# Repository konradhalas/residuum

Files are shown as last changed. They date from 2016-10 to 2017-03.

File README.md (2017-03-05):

# Residuum - line following robot



Residuum is a line following robot. It's a simple construction based on the Arduino board, an array of eight reflectance sensors and two DC motors.

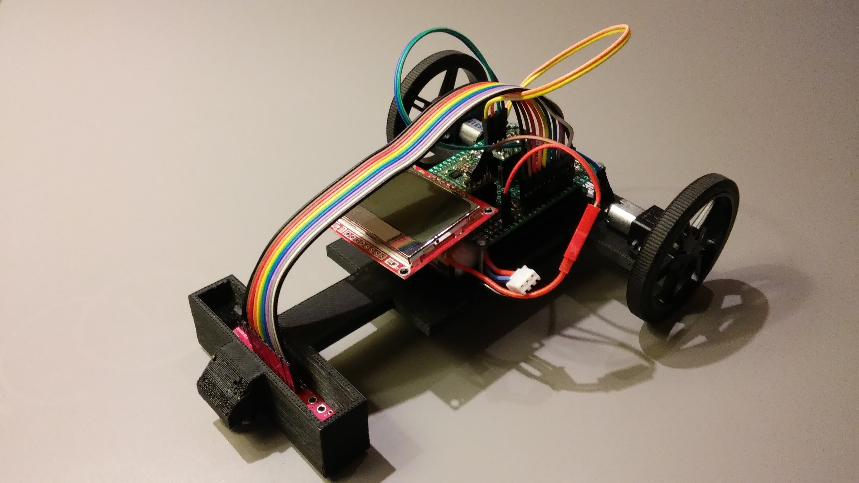
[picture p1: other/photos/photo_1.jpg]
Residuum Robot


The main goal of this project was to expedite participation in a contest of robots. Such an attitude enabled me to finish this construction in a short time (~2 months) but also resolved many of my doubts - whenever I had a few possible solutions, I chose the easier one. Of course such an approach also has its drawbacks - Residuum is definitely not a speed daemon.

The project, however, is complete and I significantly expanded my knowledge in robotics during this time. The robot contest was also a very good lesson for such beginner as I. I have many ideas that I want to implement so this is definitely not my last line follower.

Let's go briefly through all construction details.

## Electronics

*Arduino Leonardo* is a Residuum brain. I used this board because years ago I attended soldering workshops and during this event we assembled Arduino Leonardo. So it's not an original board but rather my own production. It has an *ATmega32U4* microcontroller with 32kB of flash memory, 2.5kB RAM, 1kB EEPROM, built in USB 2.0 controller and a few standard LEDs and buttons. Nothing fancy, but, more importantly in this project, it's sort of a "plug-n-play" device.

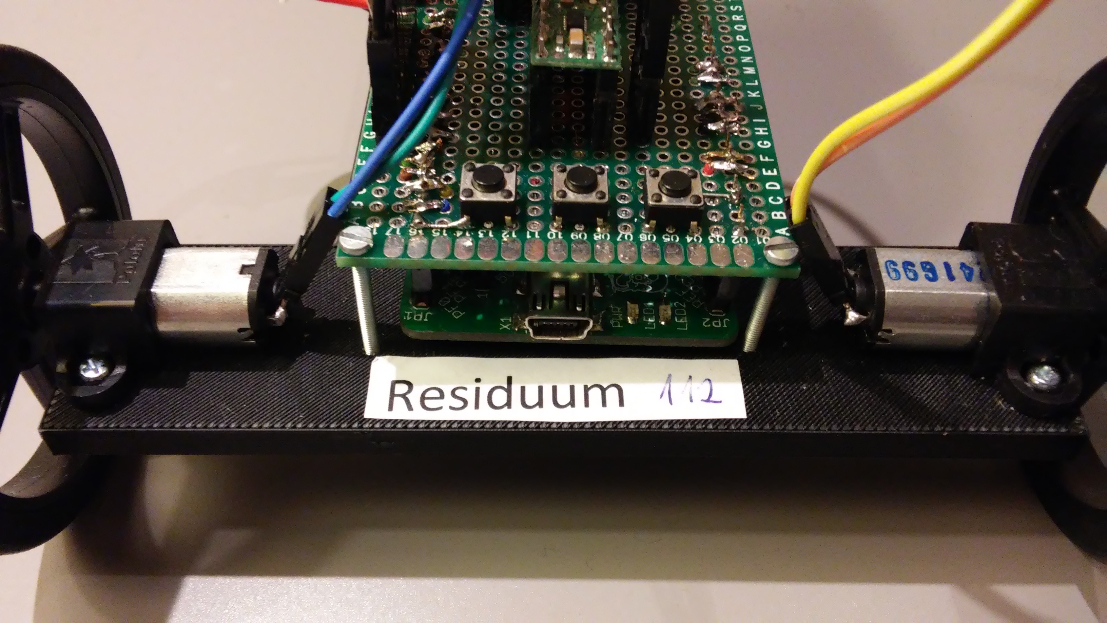
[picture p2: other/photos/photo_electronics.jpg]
electronics


Next body part - eyes. I used the *Pololu QTR-8RC* component with 8 reflectance sensors to detect a line ahead of my robot. This module is specially designed for line following robots. Moreover, the supplier provides a library for the Arduino family of boards and all you have to do is call the `readLine()` function. It’s as simple as that. Another advantage of the QTR-8RC is that it works with digital I/O pins so that a limited number of analog-to-digital converters is not a problem (e.g. my Arduino has only 6 of them).

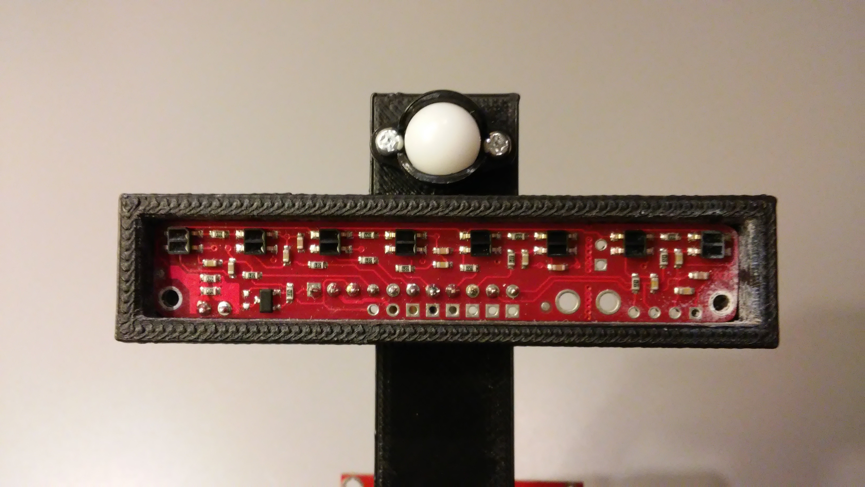
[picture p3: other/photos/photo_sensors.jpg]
sensors


Ok, so we have covered the brain and the eyes - we can see the line and we can decide where to go. Now we must move the robot in a given direction.

Residuum uses a *Pololu DRV8835 dual motor driver* to control two DC motors. This tiny H-bridge module can drive a pair of motors with standard PWM speed control and also separates the main circuit from the motor’s voltage supply.

I used a *Dualsky Li-Pol 7.4V (220mAh 25C 2S) battery* as a power source for the Residuum. My main criteria for choosing this part was weight. This battery weighs only 16g and can power my robot for a few minutes of driving. It's more than enough for the robot contest where you can change your battery for a fresh one even every single ride.

The voltage from the two-cell Li-Pol is ideal for motors but it's a bit too high for the digital part of my Residuum. I had to use a *Pololu D24V10F3 step-down voltage regulator*, which steps the 7.4V down to 3.3V.

Last but not least - LCD screen and a few tactile switches. This is the interface between me and my robot. I used a *SparkFun Graphic LCD 84x48* (which is popularly known as the screen from the Nokia 5110) to display and control all of the robot’s settings and functions.

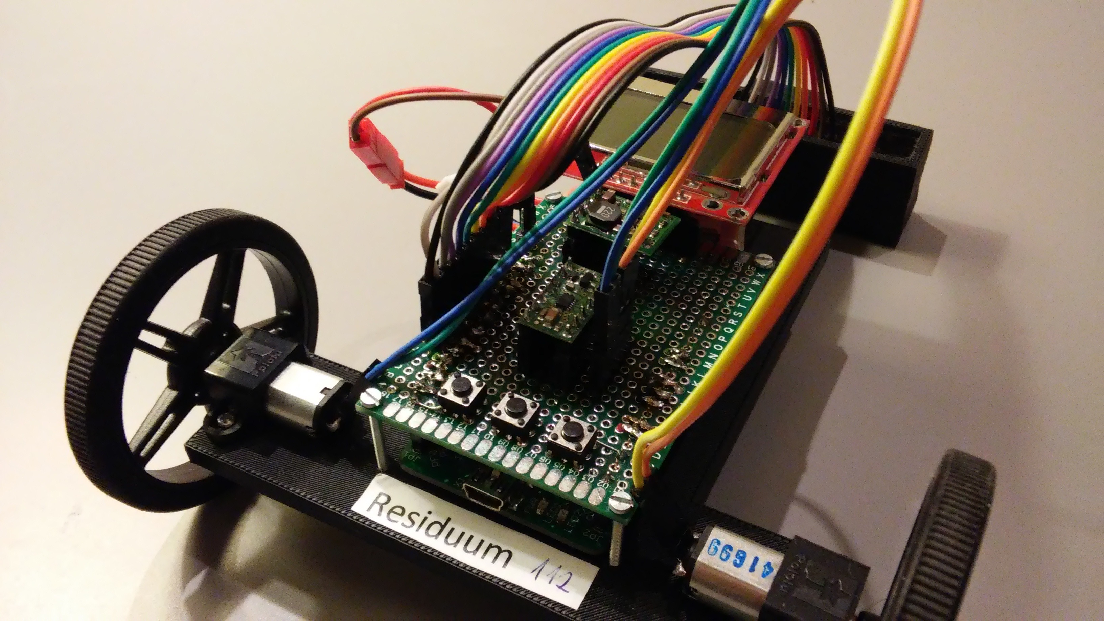
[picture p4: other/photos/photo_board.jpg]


All of these parts were soldered onto a single board in the shape of the Arduino Shield. I used a 50 x 70 mm PCB prototype matrix board, on which I soldered the following circuit:

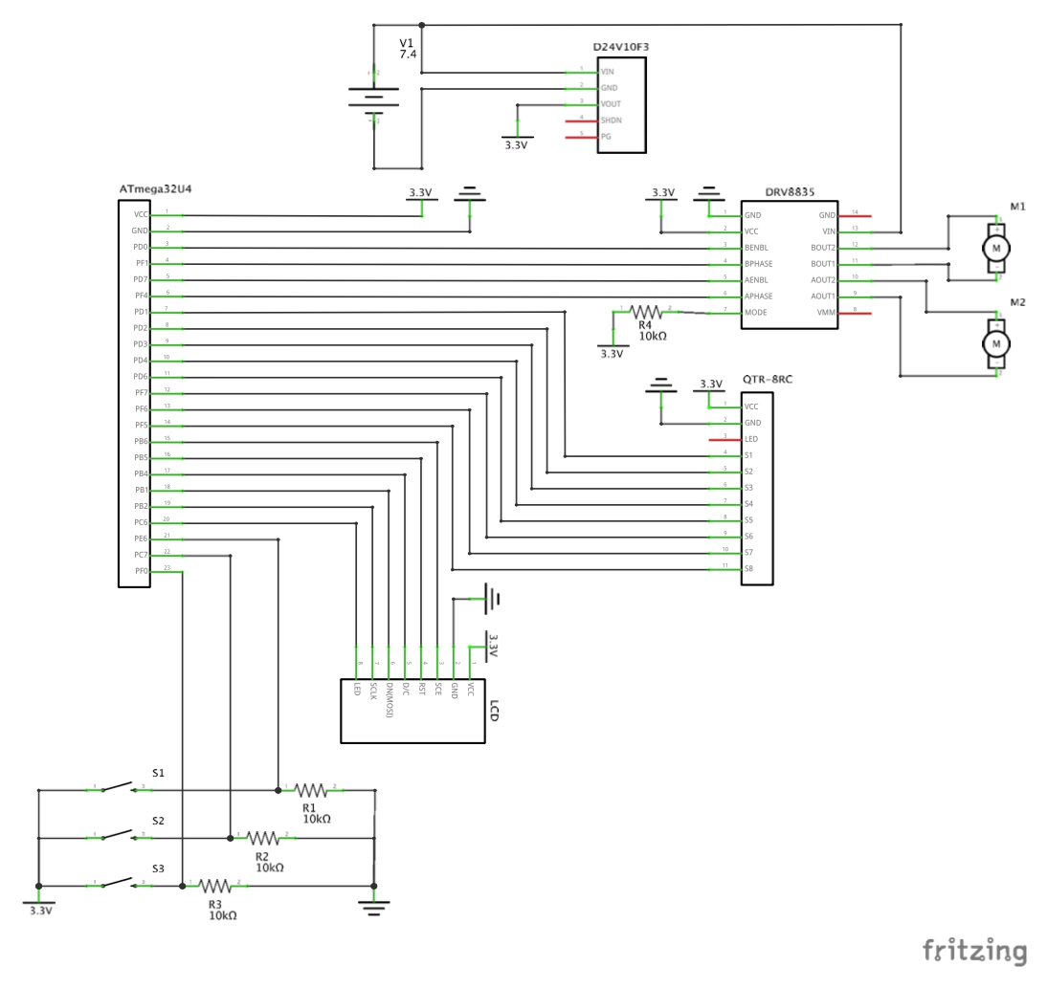
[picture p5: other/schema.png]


## Mechanics

Finally, something interesting - motors! Residuum uses two *Pololu 30:1 micro motors (Micro Metal Gearmotor MP 6V)* to move forward and change direction. To be honest, I didn't spend much time to calculate if this is the best choice in my case. I've seen that many people are using those motors, so I ordered them as well. The torque is high enough to move my construction smoothly. I also bought two *Pololu 60×8mm wheels*, *Pololu motor brackets*, and a *Pololu ball caster (3/8" Plastic Ball)* which is placed at the front of my Residuum. Buying my components from the same manufacturer assures me that everything will fit together perfectly.

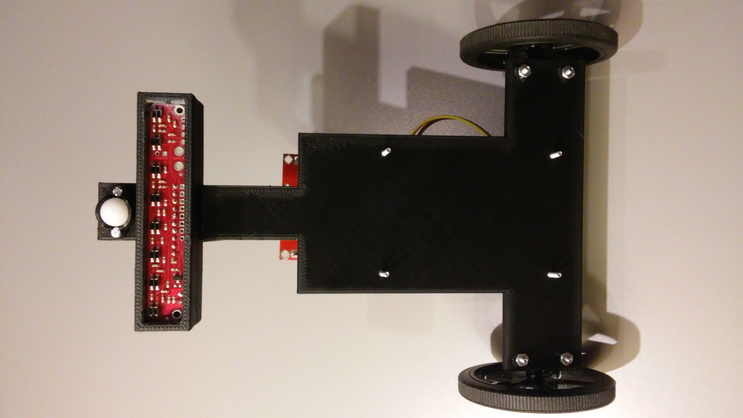
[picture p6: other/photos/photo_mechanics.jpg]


Of course all those elements have to be attached to some type of chassis. In this case I used 3D print technology. The Residuum was designed in *SketchUp* - a very simple and freely available program for 3D modeling. It took me only a few hours to prepare a model from scratch and to find somebody on [3D Hubs] (https://www.3dhubs.com/) who will print it. It's really an amazing feeling when something from your screen transform into a physical object in a matter of hours.

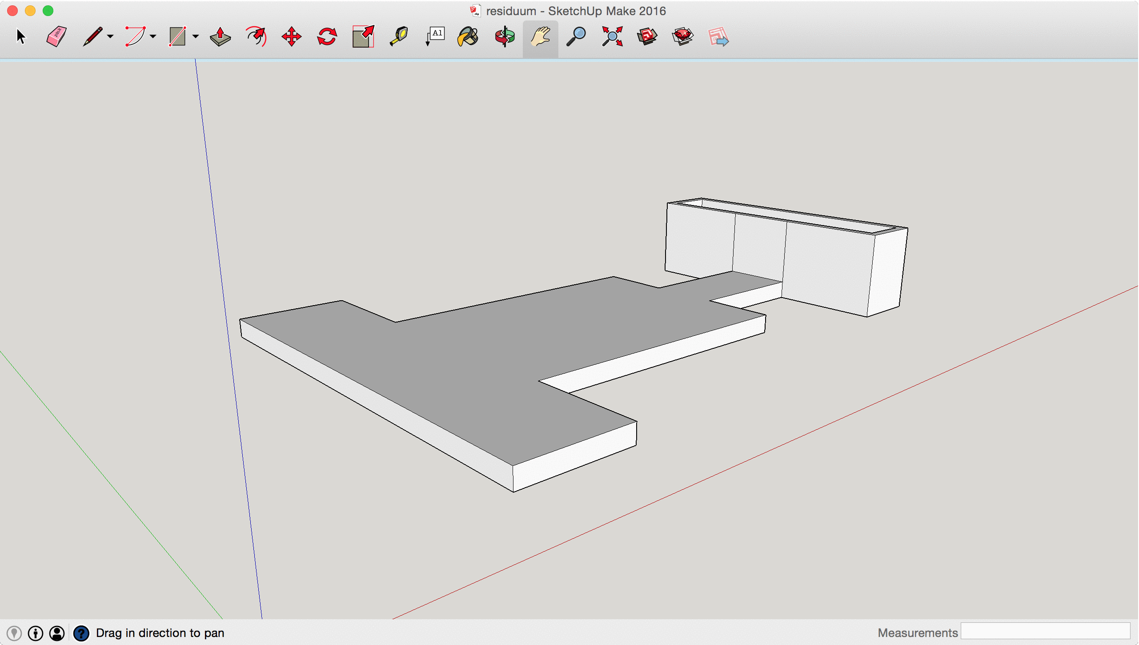
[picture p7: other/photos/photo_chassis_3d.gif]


Maybe the Residuum chassis does not follow the latest design fashions but it does combine with other parts perfectly.

## Software

The Residuum program is written in *C++*. I used the [PlatformIO](http://platformio.org/) environment to manage the build process, requirements, and testing. The *PlatformIO* toolset provides many useful features like CI integration and an *Atom* editor plugin. It really helped out quite a bit to find myself back again in the world of old-school C++.

The main ‘following’ algorithm is based on the *PID controller* and, more precisely, uses only two members, P and D. A brief example of code would serve the reader more suitably than a lengthy description.

```cpp
void Follower::follow() {
  int error = this->lineDetector.detectLine();
  int speedDelta = this->kP * error + this->kD * (error - this->lastError);
  this->lastError = error;
  this->motorsDriver.setLeftMotorSpeed(this->motorsDriver.getBaseMotorSpeed() + speedDelta);
  this->motorsDriver.setRightMotorSpeed(this->motorsDriver.getBaseMotorSpeed() - speedDelta);
}
```

The above few lines are the most important of the Residuum codebase. Let’s sprint through them. The `detectLine()` function returns `0` if the line is precisely under the middle sensor, `-X` if its under the leftmost, and `+X` if its under the rightmost. In my case (8 sensors) `X` equals 3500 (1000 per sensor), so `detectLine()` returns values between `-3500` and `3500`. When a "line error" occurs, we can calculate the delta which should be applied to our motors. I'm using here a simple version of a PD controller that calculates the motor’s speed delta based on the current error and the previous one. Finding the correct value of each member gain (`kP` and `kD`) is the trickiest part of such an algorithm. With a calculated speed delta, we can change the speed of each motor.

All settings like the `kP` and `kD` values, the motor’s base speed, etc, are available via a menu system that I implemented especially for this project. All menu items are rendered on an LCD screen and the user can move between them with tactile switches. My menu configuration looks like this:

```cpp
menu.addItem(new ActionMenuItem("FOLLOW", new FollowCommand(lineDetector, motorsDriver, EDIT_BUTTON_PIN)));
menu.addItem(new ActionMenuItem("CALIBRATE", new CalibrateCommand(qtr)));
menu.addItem(new IntegerValueMenuItem("BASE SPEED", settings.motorsBaseSpeed, new UpdateMotorsBaseSpeedCommand()));
menu.addItem(new FloatValueMenuItem("KP", settings.followerKp, FOLLOWER_KP_BASE, new UpdateFollowerKpCommand()));
menu.addItem(new FloatValueMenuItem("KD", settings.followerKd, FOLLOWER_KD_BASE, new UpdateFollowerKdCommand()));
```

During development I tried to implement all parts of the ‘OS Residuum’ program as standardized C++ libraries, without messing around with the more proprietary Arduino-specific code. This approach affords me the ability to closely test the entire codebase effortlessly in my local environment. Moreover, this code is now portable. Of course, there must be a connection between my code and the Arduino. This thin layer is realized as an implementation of a few abstract base classes that act as interfaces in my architecture.

## Parts and costs

Below you will find a list of all of Residuum’s parts and ancillary associated expenses. As I said, I didn't buy my Arduino, but I think that it should be listed here, because it's comparatively an expensive part of the robot. On the other hand, I haven’t itemized here some common (and inexpensive, as well) elements like resistors, wires, solder, etc.

* Pololu 30:1 Micro Metal Gearmotor MP 6V x 2 - 129,80 PLN
* Pololu Ball Caster with 3/8" Plastic Ball - 7,90 PLN
* Pololu QTR-8RC Reflectance Sensor Array - 39,90 PLN
* Pololu Wheel 60×8mm Pair Black - 29,90 PLN
* Pololu DRV8835 Dual Motor Driver Carrier - 17,90 PLN
* Pololu 3.3V, 1A Step-Down Voltage Regulator D24V10F3 - 30,90 PLN
* Pololu Micro Metal Gearmotor Bracket Pair Black - 18,50 PLN
* Dualsky Li-Pol 220mAh 25C 2S 7.4V - 22,90 PLN
* SparkFun Graphic LCD 84x48 - Nokia 5110 - 38,90 PLN
* PCB Prototype Matrix Board 50 x 70 mm  - 4,50 PLN
* Arduino Leonardo - 88,00 PLN
* 3D print via 3dhubs.com - 61,90 PLN

Sum: **491 PLN** (110 EUR / 125 USD)

## What's next

I achieved the main goal of this project - I took part in a robot contest, but... I placed almost last. Only two LEGO-based robots were slower than me. My best time was `13.046` while the fastest robot finished the same track in `6.683`. To me, this means that I can't upgrade Residuum. I realize now that I must build something from scratch, but this time with renewed requirements. Going forward I will focus on the robot’s weight and speed.

## Contests

One of my fastest rides from *Robocomp 2016* at Kraków, Poland:

Residuum during Robocomp 2016 (https://www.youtube.com/watch?v=713GhhHsxbs)

Residuum during *Robomaticon 2017* at Warsaw, Poland:

Residuum during Robomaticon 2017 (https://www.youtube.com/watch?v=LSfOCPmFO3o)

For this contest I upgraded Residuum a little bit. Instead of displaying all robot settings on an LCD screen and using buttons to interact with Residuum, I added a Bluetooth module (HC-08, 26,90 PLN) and implemented a simple Android application - [LF Cockpit](https://github.com/konradhalas/lf-cockpit). All Bluetooth related code is placed in `bluetooth` branch.

## Dimensions and weight

The robot dimensions:

- length: *19 cm*
- width: *14 cm*
- height: *6 cm*

The Residuum weights *166 g* with a Li-Pol battery.

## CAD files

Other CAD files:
other/residuum.skp

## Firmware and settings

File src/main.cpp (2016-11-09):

#ifndef UNIT_TEST

#include <Adafruit_GFX.h>
#include <Adafruit_PCD8544.h>
#include <QTRSensors.h>

#include "menu.h"
#include "follower.h"
#include "storage.h"

#include "consts.h"
#include "settings.h"
#include "Commands/commands.h"
#include "Menu/pcd8544renderer.h"
#include "Menu/arduinoactionsprovider.h"
#include "Follower/drv8835motorsdriver.h"
#include "Follower/qtrlinedetector.h"

Adafruit_PCD8544 display = Adafruit_PCD8544(LCD_DC_PIN, LCD_CS_PIN, LCD_RST_PIN);
PCD8544MenuRenderer renderer = PCD8544MenuRenderer(display);
ArduinoMenuActionsProvider actionsProvider = ArduinoMenuActionsProvider(NEXT_BUTTON_PIN, EDIT_BUTTON_PIN, PREVIOUS_BUTTON_PIN, STATUS_LED_PIN, BUTTONS_DELAY);
Menu menu = Menu(renderer, actionsProvider, HANDLE_TICK_FREQUENCY);

QTRSensorsRC qtr = QTRSensorsRC((unsigned char[]) {RS_1_PIN, RS_2_PIN, RS_3_PIN, RS_4_PIN, RS_5_PIN, RS_6_PIN, RS_7_PIN,RS_8_PIN}, NUMBER_OF_REFLECTANT_SENSORS);

DRV8835MotorsDriver motorsDriver = DRV8835MotorsDriver(MOTOR_LEFT_PHASE, MOTOR_LEFT_ENABLE, MOTOR_RIGHT_PHASE, MOTOR_RIGHT_ENABLE, BASE_MOTOR_SPEED);
QtrLineDetector lineDetector = QtrLineDetector(qtr, NUMBER_OF_REFLECTANT_SENSORS);

void indicateSetupFinish() {
  pinMode(STATUS_LED_PIN, OUTPUT);
  digitalWrite(STATUS_LED_PIN, HIGH);
  delay(BUTTONS_DELAY);
  digitalWrite(STATUS_LED_PIN, LOW);
}

void setup()   {
  Settings settings;

  if (digitalRead(EDIT_BUTTON_PIN) == HIGH) {
    Storage<Settings>::save(settings);
  } else {
     settings = Storage<Settings>::load();
  }

  renderer.setup(LCD_LED_PIN, settings.lcdContrast, settings.lcdBakclight);

  motorsDriver.setup();

  menu.addItem(new ActionMenuItem("FL", new FollowCommand(lineDetector, motorsDriver, EDIT_BUTTON_PIN)));
  menu.addItem(new ActionMenuItem("CL", new CalibrateCommand(qtr)));
  menu.addItem(new FloatValueMenuItem("KP", settings.followerKp, FOLLOWER_KP_BASE, new UpdateFollowerKpCommand()));
  menu.addItem(new FloatValueMenuItem("KD", settings.followerKd, FOLLOWER_KD_BASE, new UpdateFollowerKdCommand()));
  menu.addItem(new IntegerValueMenuItem("BS", settings.motorsBaseSpeed, new UpdateMotorsBaseSpeedCommand()));
  menu.addItem(new IntegerValueMenuItem("LI", 0, NULL, new ReadLineCommand(lineDetector)));
  menu.addItem(new ActionMenuItem("MT", new MotorCheckCommand(motorsDriver, MOTOR_BOTH)));
  menu.addItem(new IntegerValueMenuItem("FT", settings.followTimeout / MS, new UpdateFollowTimeoutCommand()));

  indicateSetupFinish();
}

void loop() {
  menu.handle();
}

#endif

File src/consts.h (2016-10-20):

#define MS 1000
#define S(val) val * MS

#define NEXT_BUTTON_PIN 7 // PE6
#define EDIT_BUTTON_PIN 13 // PC7
#define PREVIOUS_BUTTON_PIN 23 // PF0

#define LCD_LED_PIN 5 // PC6
#define LCD_DC_PIN 8 // PB4
#define LCD_CS_PIN 10 // SCE, PB6
#define LCD_RST_PIN 9 // PB5

#define STATUS_LED_PIN 11

#define RS_1_PIN 2  // PD1
#define RS_2_PIN 0  // PD2
#define RS_3_PIN 1  // PD3
#define RS_4_PIN 4  // PD4
#define RS_5_PIN 12 // PD6
#define RS_6_PIN 18 // PF7
#define RS_7_PIN 19  // PF6
#define RS_8_PIN 20 // PF5

#define BUTTONS_DELAY 500
#define LCD_CONTRAST 55
#define LCD_BAKCLIGHT false
#define NUMBER_OF_REFLECTANT_SENSORS 8
#define HANDLE_TICK_FREQUENCY 20000

#define MOTOR_LEFT 0
#define MOTOR_RIGHT 1
#define MOTOR_BOTH 2
#define MOTOR_LEFT_ENABLE  3  // PD0 (PWM)
#define MOTOR_LEFT_PHASE   22 // PF1
#define MOTOR_RIGHT_ENABLE 6  // PD7 (PWM)
#define MOTOR_RIGHT_PHASE  21 // PF4

#define BASE_MOTOR_SPEED 120
#define MOTOR_CHECK_TIMEOUT S(3)

#define FOLLOW_TIMEOUT S(30)
#define FOLLOW_START_TIMEOUT S(1)

#define FOLLOWER_KP 0.05
#define FOLLOWER_KD 1.0

#define FOLLOWER_KP_BASE 100
#define FOLLOWER_KD_BASE 10

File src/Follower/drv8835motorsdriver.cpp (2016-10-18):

#ifndef UNIT_TEST

#include <Arduino.h>

#include "drv8835motorsdriver.h"

DRV8835MotorsDriver::DRV8835MotorsDriver(int leftMotorPhasePin, int leftMotorEnablePin, int rightMotorPhasePin, int rightMotorEnablePin, int baseSpeed): leftMotorPhasePin(leftMotorPhasePin), leftMotorEnablePin(leftMotorEnablePin), rightMotorPhasePin(rightMotorPhasePin), rightMotorEnablePin(rightMotorEnablePin), baseSpeed(baseSpeed) {

}

void DRV8835MotorsDriver::setup() {
  pinMode(this->leftMotorEnablePin, OUTPUT);
  pinMode(this->leftMotorPhasePin, OUTPUT);
  digitalWrite(this->leftMotorEnablePin, LOW);
  digitalWrite(this->leftMotorPhasePin, LOW);
  pinMode(this->rightMotorEnablePin, OUTPUT);
  pinMode(this->rightMotorPhasePin, OUTPUT);
  digitalWrite(this->rightMotorEnablePin, LOW);
  digitalWrite(this->rightMotorPhasePin, LOW);
}

void DRV8835MotorsDriver::setLeftMotorSpeed(int speed) {
  this->setSpeed(this->leftMotorPhasePin, this->leftMotorEnablePin, speed);
}

void DRV8835MotorsDriver::setRightMotorSpeed(int speed) {
  this->setSpeed(this->rightMotorPhasePin, this->rightMotorEnablePin, speed);
}

int DRV8835MotorsDriver::getBaseMotorSpeed() {
  return this->baseSpeed;
}

void DRV8835MotorsDriver::setBaseMotorsSpeed(int speed) {
  this->baseSpeed = speed;
}

void DRV8835MotorsDriver::setSpeed(int phasePin, int enablePin, int speed) {
  digitalWrite(phasePin, speed > 0 ? HIGH : LOW);
  if (speed < 0) {
    speed = - speed;
  }
  if (speed > 255) {
    speed = 255;
  }
  analogWrite(enablePin, speed);
}

#endif

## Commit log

2016-09-28 Draft of motors setup
2016-09-28 Refactor motors code a litle bit
2016-09-30 Pre PID
2016-10-01 Add basic PID
2016-10-15 Small changes intruduced during soldering
2016-10-18 PID setup tool
2016-10-30 Improve chassis gif
2016-10-30 Add 3d model
    [residuum.skp]
2016-11-09 Fix Travis - part VIII
    [main.cpp]
2016-11-09 Fix Travis - part XIV
    [main.cpp]
2016-11-09 Fix Travis - part XVIII
    [main.cpp]
